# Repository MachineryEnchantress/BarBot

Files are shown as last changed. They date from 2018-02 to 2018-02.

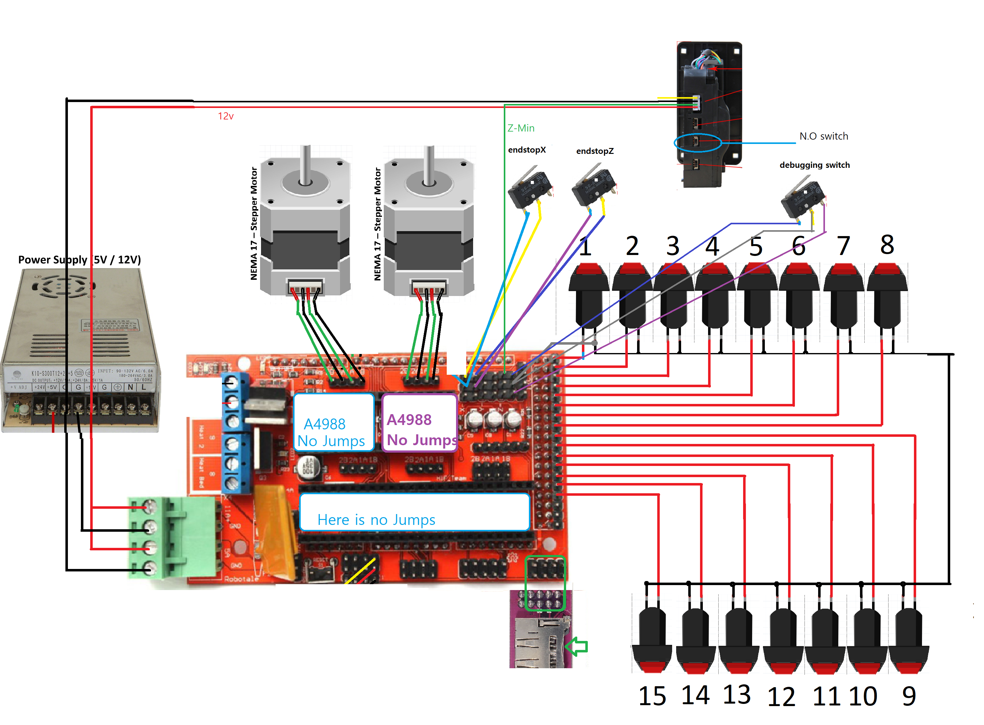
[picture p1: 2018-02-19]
Wiring Diagram.png

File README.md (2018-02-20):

# Naomi Wu's BarBot
An Automated Bartender powered by Arduino  
BarBot

Based on the work of Lukas Šidlauskas:  
https://create.arduino.cc/projecthub/sidlauskas/barbot-cocktail-mixing-robot-0318aa  
https://github.com/sidlauskaslukas/barbot

[BarBot Build Video 1](https://youtu.be/aKa0YGDu1KI)  
BarBot Build Video 1  

[BarBot Build Video 2](https://youtu.be/N1LVktHzpnw)  
BarBot Build Video 2  

[BarBot Build Video 3- Demo](https://youtu.be/aPoAVoNNvHs)  
BarBot Build Video 3

## About

For my BarBot I wanted to make sure it was rock-solid reliable in a crowded bar environment so eliminated the touchscreen menus and wireless connectivity present in other versions of this project. Nearly any error can be dealt with by simply power cycling the device. Since there is no Raspberry Pi or SBC there is no risk of corruption when this is done. 

16 popular drinks (15 alcoholic and 1 non-alcoholic for non-drinkers and so that children can participate with supervision) are available from 16 arcade style buttons. A printed menu lists what button number corresponds to which drink.

Since the BarBot is designed for a working bar- and yes even in Shenzhen we are subject to surprise health inspections I had to do without pumps or difficult to clean feed lines. All of the components that require nightly cleaning are the same that bar staff are already accustomed to cleaning- spirit measures and bar mats. All drive components and bearings have been moved from under the pour spouts to well above or behind so there is no risk of an accumulation of sugar-rich liquids gumming up hard to clean moving parts of the machine or attracting vermin.

This BarBot is a functional novelty- it's something fun for visitors to play with. Perfect for my home city of Shenzhen where a large number of patrons are tech professionals. It is not secured for true commercial use- and with a bar full of half-drunk hardware engineers it would be pointless to try. In this case, it's better to rely on good faith then pretend you could stop them if challenged. Patrons could still manually press their cups to the spirit measures to manually dispense alcohol if they wanted to- but they could also reach over the bar and steal liquor while the bartender's back was turned. So far none have because why ruin the fun when there's no "hack" in doing so? If you really wanted to, a clear acrylic panel could be added to the front to prevent any manual dispensing, but it's really a lot less fun that way.

Portion control and payment is handled via an inexpensive arcade token acceptor. A customer can pay the bartender for a cup of ice and a token. When the correct token is inserted into the BarBot a contact is momentarily closed. The customer then has 60 seconds to press a drink selection button. That same contact can be closed with the key switch, in which case no tokens are needed for any orders while the switch is in that position.

Barbots of this configuration typically use either a servo or a stepper motor with a lead screw to depress the spirit measure spout depending on the type of dispenser it is. My code changes allow for either as RAMPS boards can control both steppers and a servo.

In the build and demonstration videos, you'll see that the full 25ml "shot" the spirit measure contains is usually only partially dispensed. This is because the actual shot size is defined in the code as a function of how long the spout is depressed. This allows for finer tuning of the drink flavor and portion size which would not be possible if only 25ml increments were used.

This BarBot was designed to be easy to build with off-the-shelf OpenBuilds components, V-Slot aluminum extrusion, and low-cost 3D printer parts. The heart of the BarBot is a standard Arduino Mega, RAMPS 1.4/1.5 and A4988 stepper driver combination as used in many 3D printers.

BarBot<BR>
See [Build Guide](https://github.com/sexycyborg/BarBot/blob/master/BarBotDrwMk01.PDF). 
  *Guide and SolidWorks CAD drawings courtesy of [Vexelius](https://www.thingiverse.com/Vexelius/).*

## BOM
[1x Arduino Mega 2560](http://reprap.org/wiki/Arduino_Mega)  
[1x RAMPS 1.4](http://reprap.org/wiki/RAMPS_1.4)/[1.5](http://reprap.org/wiki/RAMPS_1.5)  
[2x A4988 Stepper Driver](http://reprap.org/wiki/A4988)  
[Available as a kit](https://www.gearbest.com/kits/pp_228312.html?lkid=11066669)

1x [RAMPS 1.4/1.5 SD Card Reader](http://amzn.to/2EYiyeb)

[10x10 Drag Chain](http://amzn.to/2ECHM3W)  
 2 Meters 

[V-Slot® 20x80 Linear Rail](http://openbuildspartstore.com/v-slot-20x80-linear-rail/)  
 3x1200mm (Two vertical risers and one horizontal carriage rail)  
 2x1160mm (Lower brace, shelf for bar mat)

[V-Slot® 20x40 Linear Rail](http://openbuildspartstore.com/v-slot-20x40-linear-rail/)  
1x 1200mm (Horizontal rail for drag chain)  
2x 600mm (Horizontal legs)

1x [V-Slot® NEMA 17 Linear Actuator Bundle](http://openbuildspartstore.com/v-slot-nema-17-linear-actuator-bundle-lead-screw/)  
500mm (400mm is better if you can get it or make it yourself)

1x [V-Slot Gantry Set](http://openbuildspartstore.com/v-slot-gantry-set/)  
20mm - 80mm (Universal)  
Delrin Solid V Wheels

1x [Motor Mount Plate - NEMA 17 Stepper Motor](http://openbuildspartstore.com/motor-mount-plate-nema-17-stepper-motor/)

1x [Idler Pulley Plate](http://openbuildspartstore.com/idler-pulley-plate/)

1x [Smooth Idler Pulley Kit](http://openbuildspartstore.com/smooth-idler-pulley-kit/)  

[GT2-2M Timing Belt](http://openbuildspartstore.com/gt2-2m-timing-belt/)  
3 Meters

1x [GT2-2M Timing Pulley - 20 Tooth](http://openbuildspartstore.com/gt2-2m-timing-pulley-20-tooth/)

2x [NEMA 17 Stepper Motor](http://openbuildspartstore.com/nema-17-stepper-motor/)  

30x [Black Angle Corner Connector](http://openbuildspartstore.com/black-angle-corner-connector/)

[Openbuilds Low Profile Screws](http://openbuildspartstore.com/low-profile-screws-m5/)  
60x M5\*8  
4x M5\*40  
6x M5\*25  
4x M5\*15  

[Aluminum Spacer](http://openbuildspartstore.com/aluminum-spacers/)  
4x 3mm  
4x 6mm 

50x [Tee Nuts](http://openbuildspartstore.com/tee-nuts-25-pack/)

50x [Drop In Tee Nuts](http://openbuildspartstore.com/drop-in-tee-nuts/) 

30x [Nylon Insert Hex Locknut - M5](http://openbuildspartstore.com/nylon-insert-hex-locknut-m5/)  

[Slot Cover™ / Panel Holder](http://openbuildspartstore.com/slot-cover-panel-holder/)  
1250mm

2x [Bar mat](http://amzn.to/2Eo2QvR)

#### Control Box
[V-Slot® 20x20 Linear Rail](http://openbuildspartstore.com/v-slot-20x20-linear-rail/)  
530mm x 4  
165mm x 5  
130mm x 4  
(All with 5mm threaded ends)

8x [Cube Corner Connector](http://openbuildspartstore.com/cube-corner-connector/)  

25x M5*15 [Openbuilds Low Profile Screws](http://openbuildspartstore.com/low-profile-screws-m5/)

1x [Coin Acceptor](https://item.taobao.com/item.htm?id=540305747207)  
(Or similar if you modify the lower lasercut panel to fit)  

16x [27x27 Illuminated Arcade Buttons](https://www.aliexpress.com/store/product/27-27mm-quadrate-LED-Light-Illuminated-Full-Colors-Push-Button-With-Micro-Switch-Master-Arcade-DIY/1960309_32559164401.html)

1x [22mm Emergency Stop Push Button Switch 12V DC LED Illuminated (or similar)](http://amzn.to/2Chvvgb)

1x [22mm Key Selector Switch](http://amzn.to/2ErJs0M)

1x [Power Socket Switch IEC 320 C14](http://amzn.to/2HcuYjs)

1x [12v Power Supply, 150w (Part No. MS-150-12 or similar)](https://www.aliexpress.com/item/MS-150-12-mini-size-12-5a-led-psu-150w-12v-power-supply/32663431069.html)

1x [Ribbon cable to 18 pin connector 40CM long (Optional but helpful)](https://item.taobao.com/item.htm?id=520267411024)

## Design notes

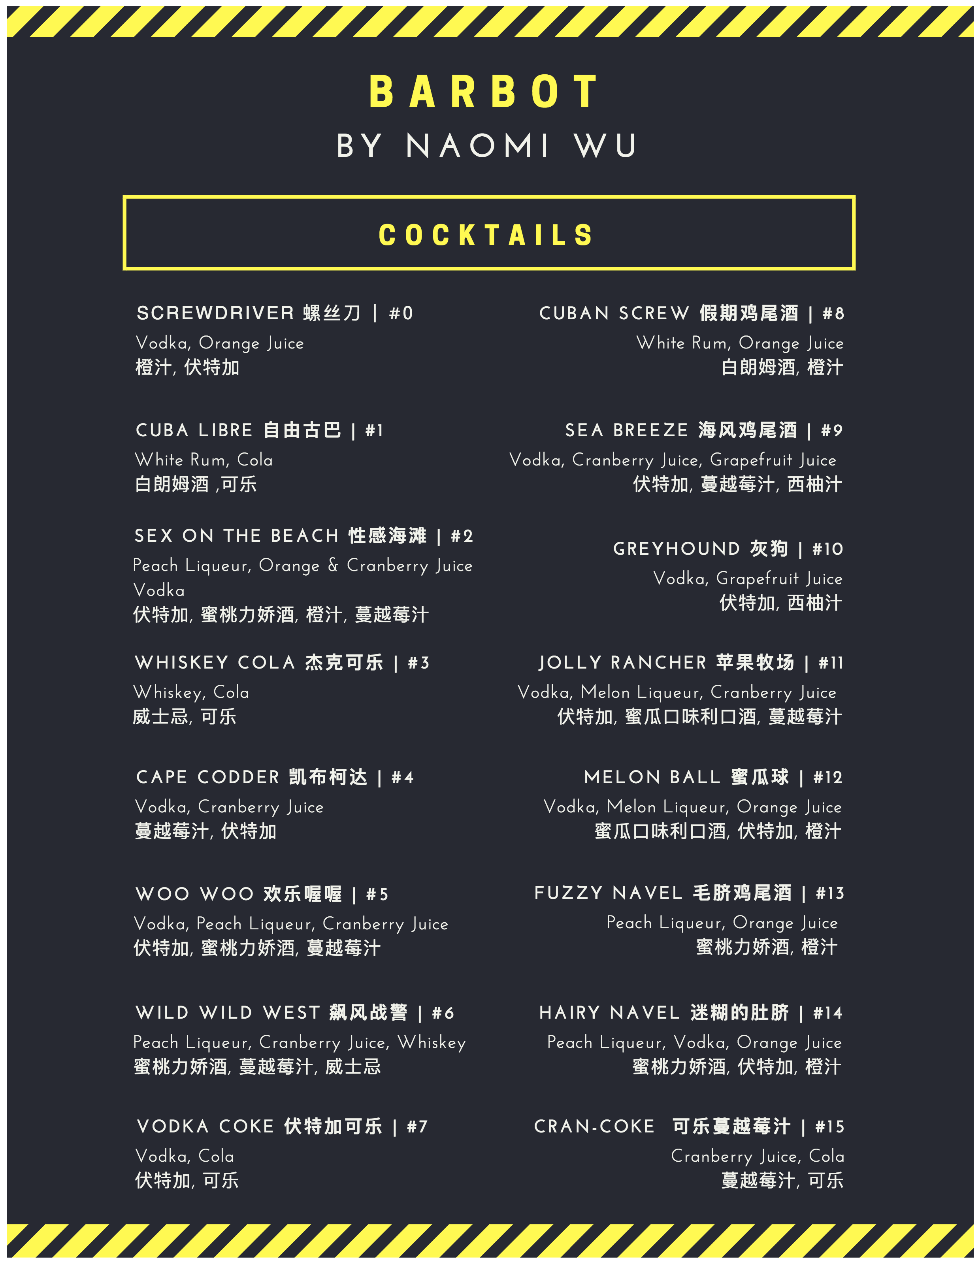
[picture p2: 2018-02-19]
Menu.png

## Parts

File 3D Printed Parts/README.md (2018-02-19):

# Naomi Wu's BarBot
An Automated Bartender powered by Arduino  

All parts can be printed in PLA at 2mm layer height, 30% infill.

## Additional 3D Files Required:

[Quick Release RAMPS Holder for T-Slot Profile](https://www.thingiverse.com/thing:2169986)  

[2020 Cable Zip Tie Mount for M5x10 screws (optional fins)](https://www.thingiverse.com/thing:2486032)

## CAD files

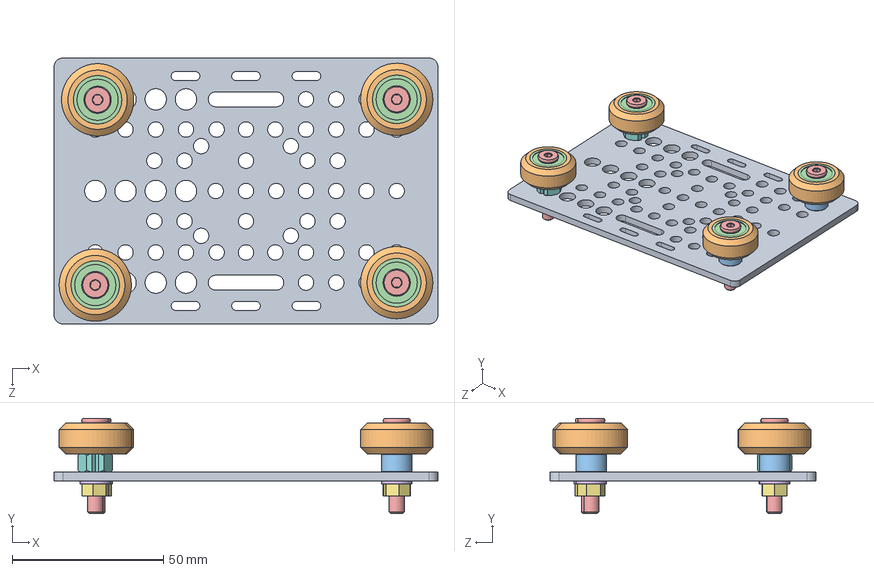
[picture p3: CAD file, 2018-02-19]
SolidWorks/Dispenser Carriage.SLDASM
127.0 x 31.5 x 88.0 mm
V-Slot Gantry Plate 20-80mm
Solid V Wheel x 4
Aluminum Spacer 6mm x 2
Ball Bearing 5 x 16 x 5 x 8
Low Profile Screw M5 x 4
STDWasher x 4
STDNut x 4
Eccentric Spacer 6mm x 2

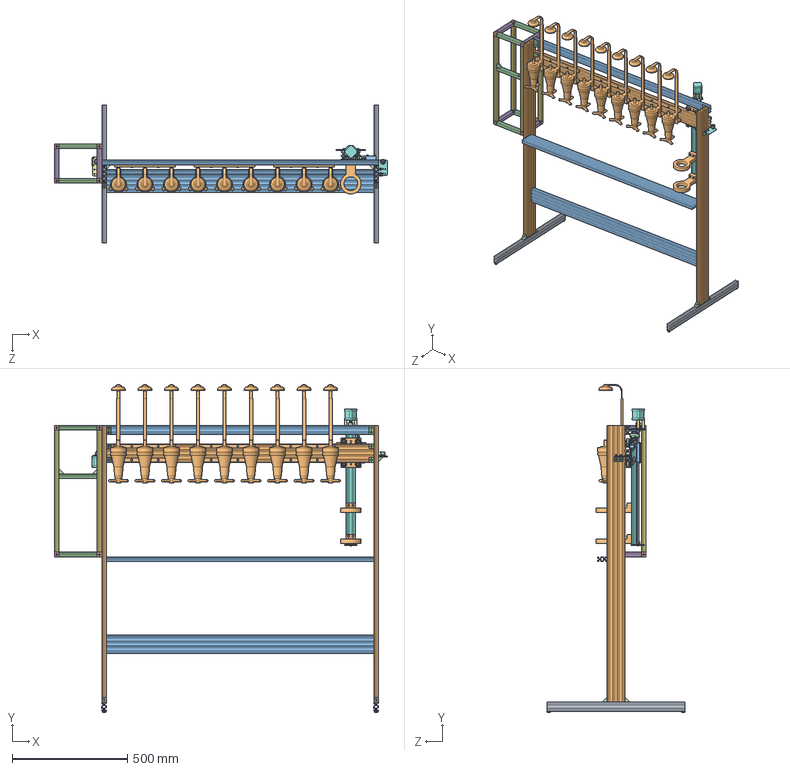
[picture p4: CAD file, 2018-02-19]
SolidWorks/BarBot.SLDASM
1444.5 x 1423.2 x 600.0 mm
V-Slot 20x40x600 x 2
V-Slot 20x80x1200 x 3
V-Slot 20x40x1200
Black Angle Corner Connector x 20
Tee Nut x 12
Low Profile Screw M5 x 42
RubberPad x 4
Idler Pulley Plate
STDNut x 12
STDWasher x 12
Aluminum Spacer 6mm x 7
Smooth Idler Pulley Wheel
Ball Bearing 5 x 16 x 5 x 18
Nylon Spacer 0.125in
Motor Mount Plate Nema 17
Nema 17 Stepper Motor x 2
GT2 Timing Pulley 20 Tooth
Bar Butler x 3
V-Slot 20x80x1160 x 2
V-Slot 20x20x165 x 5
Cube Corner Connector x 8
V-Slot 20x20x130 x 4
V-Slot 20x20x530 x 4
Self Tapping Screw x 4
Socket Head Cap Screw M3 x 3
Nylon Insert Lock Nut M5 x 6
Threaded Rod Plate Nema 17 x 2
Ball Bearing 8 x 16 x 5 x 2
Shim Washer 8mm x 2
Lock Collar 8mm x 2
Aluminum Spacer 1.5in x 3
Flexible Coupling 5mm x 8mm
8mm leadscrew 520mm
V-Slot Gantry Plate 20-80mm x 2
Spacer Block x 2
Solid V Wheel x 8
Precision Shim 10 x 5 x 1 x 8
8mm Acme Nut Block
Eccentric Spacer 6mm x 2
V-Slot 20x40x500 Linear Rail
Aluminum Spacer 3mm x 8
CupRing x 2
XAxis Endstop Holder
RAMPSEndStop x 2
Button Head Socket Cap Screw M3 x 4
ZAxis Endstop Holder

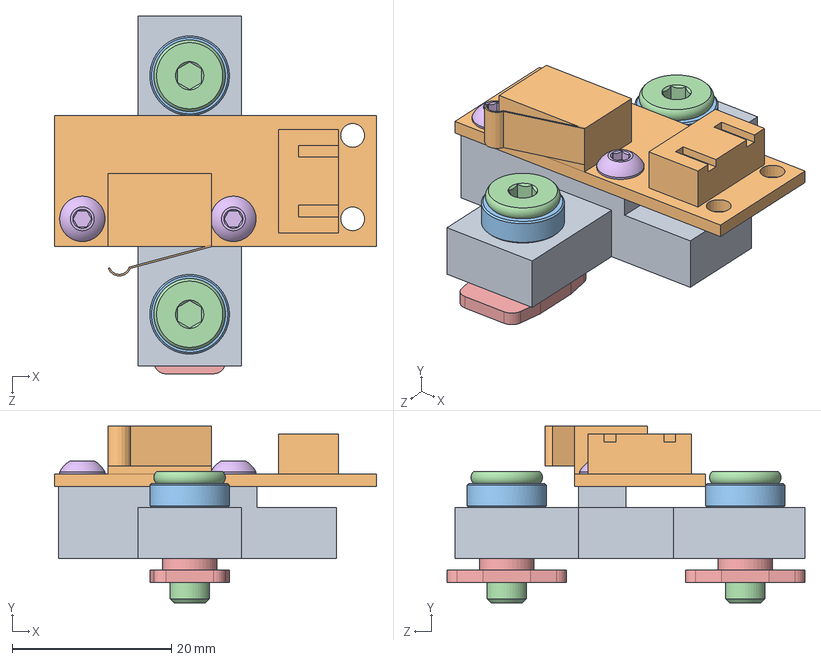
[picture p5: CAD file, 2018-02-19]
SolidWorks/Z-Axis Endstop.SLDASM
40.5 x 22.2 x 45.0 mm
ZAxis Endstop Holder
RAMPSEndStop
Aluminum Spacer 3mm x 2
Low Profile Screw M5 x 2
Tee Nut x 2
Button Head Socket Cap Screw M3 x 2

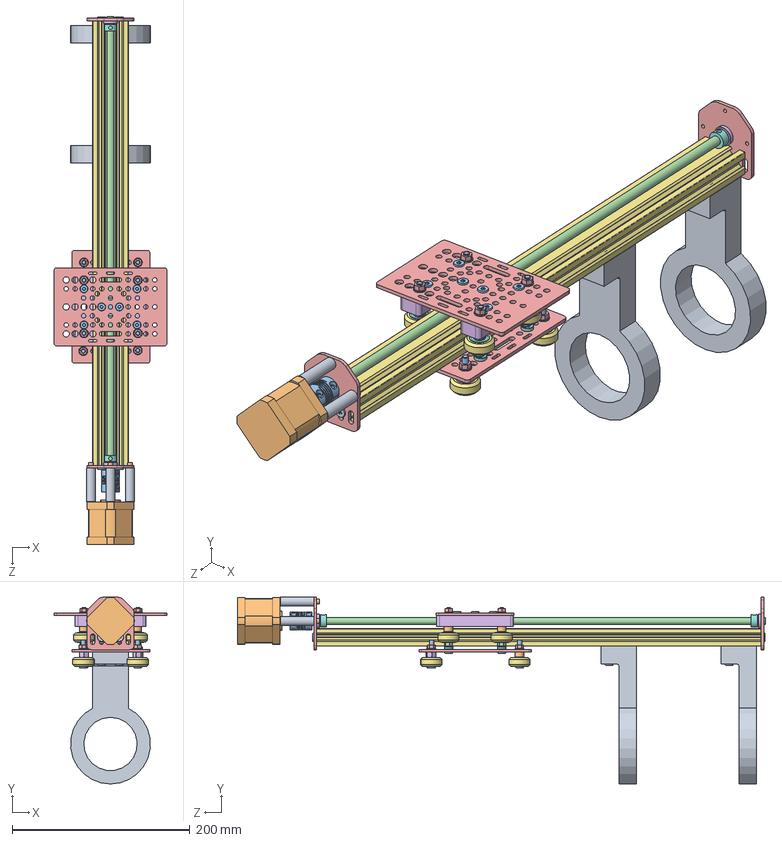
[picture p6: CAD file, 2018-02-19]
SolidWorks/Dispenser Actuator.SLDASM
127.0 x 210.3 x 594.1 mm
Self Tapping Screw x 4
Socket Head Cap Screw M3 x 3
Low Profile Screw M5 x 18
Nylon Insert Lock Nut M5 x 6
Threaded Rod Plate Nema 17 x 2
Ball Bearing 8 x 16 x 5 x 2
Shim Washer 8mm x 2
Lock Collar 8mm x 2
Aluminum Spacer 1.5in x 3
Nema 17 Stepper Motor
Flexible Coupling 5mm x 8mm
8mm leadscrew 520mm
V-Slot Gantry Plate 20-80mm x 2
Spacer Block x 2
Solid V Wheel x 8
Ball Bearing 5 x 16 x 5 x 16
Precision Shim 10 x 5 x 1 x 8
Aluminum Spacer 6mm x 6
8mm Acme Nut Block
STDWasher x 8
STDNut x 8
Eccentric Spacer 6mm x 2
V-Slot 20x40x500 Linear Rail
Aluminum Spacer 3mm x 4
CupRing x 2
Tee Nut x 4

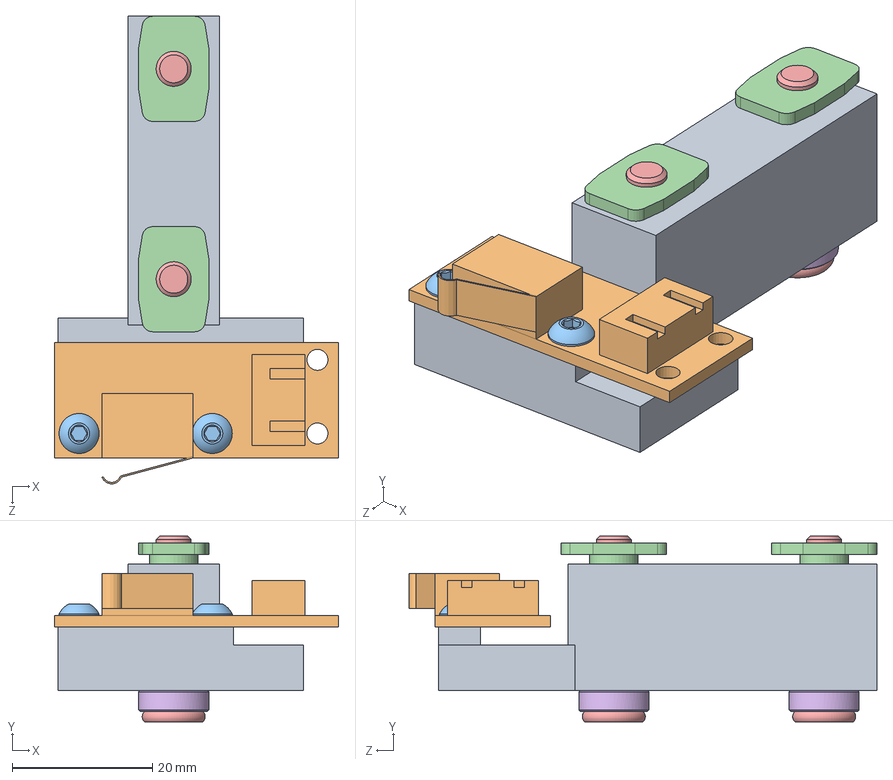
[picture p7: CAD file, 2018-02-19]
SolidWorks/X-Axis Endstop.SLDASM
40.5 x 26.5 x 66.7 mm
XAxis Endstop Holder
RAMPSEndStop
Button Head Socket Cap Screw M3 x 2
Tee Nut x 2
Low Profile Screw M5 x 2
Aluminum Spacer 3mm x 2

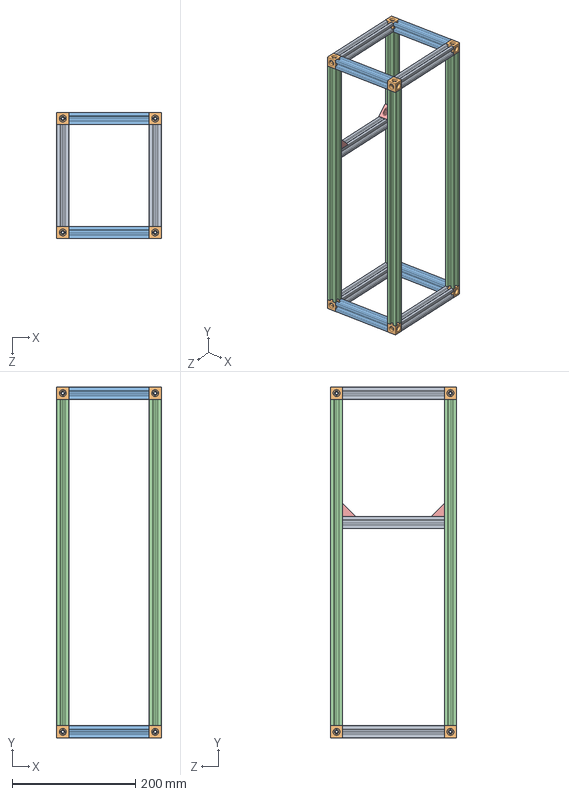
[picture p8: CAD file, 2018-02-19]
SolidWorks/Control Box.SLDASM
170.0 x 570.0 x 205.0 mm
V-Slot 20x20x165 x 5
Cube Corner Connector x 8
V-Slot 20x20x130 x 4
V-Slot 20x20x530 x 4
Black Angle Corner Connector x 2

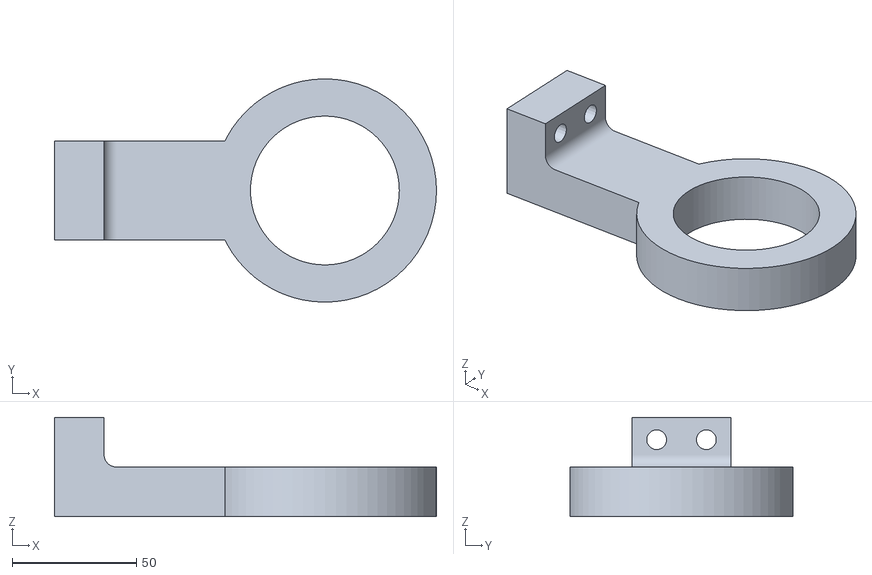
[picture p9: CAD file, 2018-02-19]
3D Printed Parts/Cup Ring.stl
154.0 x 90.0 x 40.0

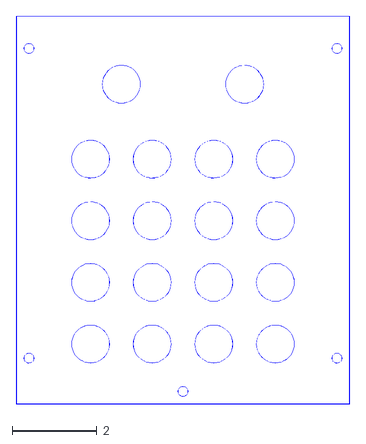
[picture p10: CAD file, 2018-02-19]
Laser Cut Panels/233mm x 200mm- Upper Front v1.dxf
7.88 x 9.17

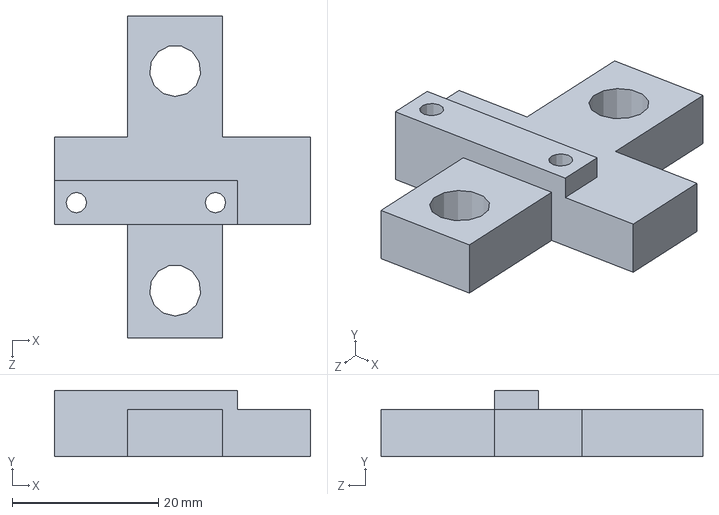
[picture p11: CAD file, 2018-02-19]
SolidWorks/ZAxis Endstop Holder.SLDPRT
35.0 x 9.05 x 44.0 mm

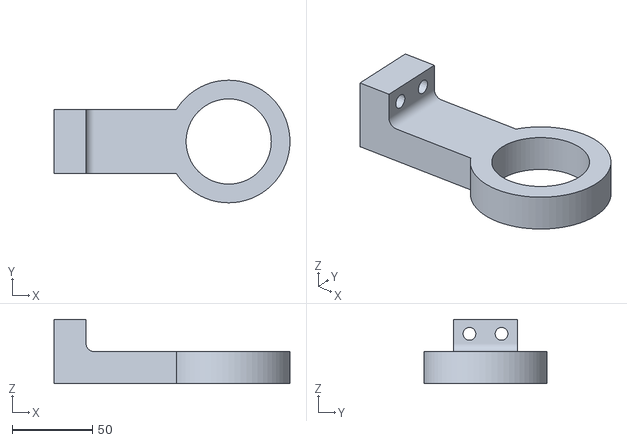
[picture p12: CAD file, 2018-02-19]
3D Printed Parts/Spirit Measure Ring.stl
147.2 x 76.5 x 40.0

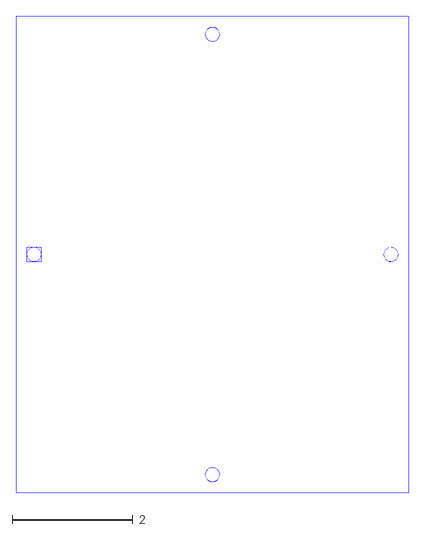
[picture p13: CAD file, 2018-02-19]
Laser Cut Panels/200mm x 165mm- Top v1.dxf
6.50 x 7.88

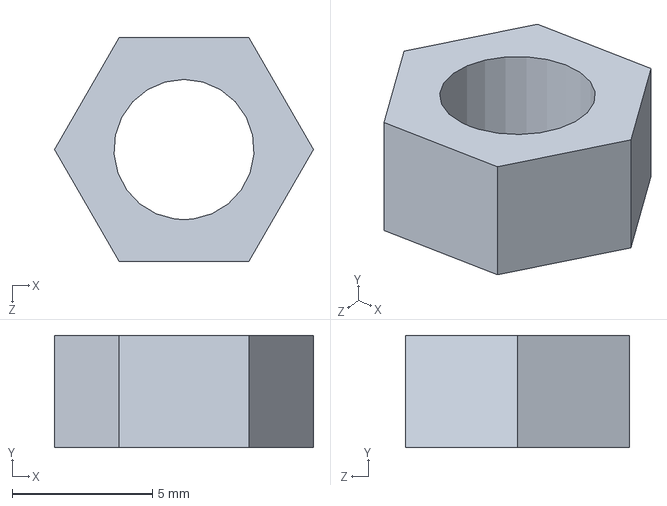
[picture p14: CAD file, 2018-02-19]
SolidWorks/STDNut.SLDPRT
9.24 x 4.00 x 8.00 mm

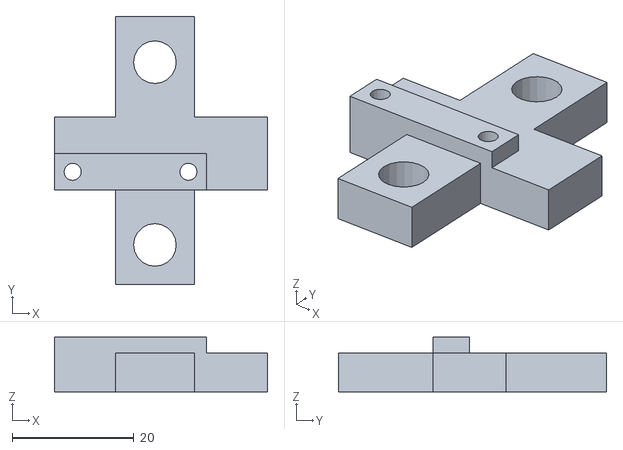
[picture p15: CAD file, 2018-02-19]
3D Printed Parts/Z-Axis End-Stop Switch Holder.stl
35.0 x 44.0 x 9.00

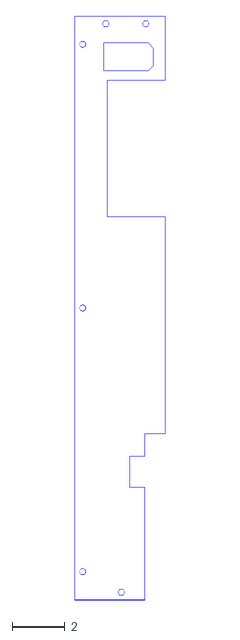
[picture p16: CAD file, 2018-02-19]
Laser Cut Panels/565mm x 87.5mm Rear Side v2.dxf
3.45 x 22.2

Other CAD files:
SolidWorks/XAxis Endstop Holder.SLDPRT
3D Printed Parts/Z-Axis Motor Drag Chain Attachment.stl
Laser Cut Panels/332mm x 200mm- Front Lower v1.dxf
3D Printed Parts/X-Axis End-Stop Switch Holder.stl
Laser Cut Panels/565mm x 165mm- Side v1.dxf
Laser Cut Panels/565mm x 200mm- Back v1.dxf
SolidWorks/BarBot.SLDPRT
SolidWorks/CupRing.SLDPRT
SolidWorks/RAMPSEndStop.SLDPRT
SolidWorks/RubberPad.SLDPRT
SolidWorks/STDWasher.SLDPRT
SolidWorks/V-Slot 20x20x130.SLDPRT
SolidWorks/V-Slot 20x20x165.SLDPRT
SolidWorks/V-Slot 20x20x530.SLDPRT
SolidWorks/V-Slot 20x40x1200.SLDPRT
SolidWorks/V-Slot 20x40x600.SLDPRT
SolidWorks/V-Slot 20x80x1160.SLDPRT
SolidWorks/V-Slot 20x80x1200.SLDPRT

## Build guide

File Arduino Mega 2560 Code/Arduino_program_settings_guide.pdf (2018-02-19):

BARBOT Arduino setting Guide.

1. Install the Arduino IDE.
2. Install necessary libraries to the Arduino IDE

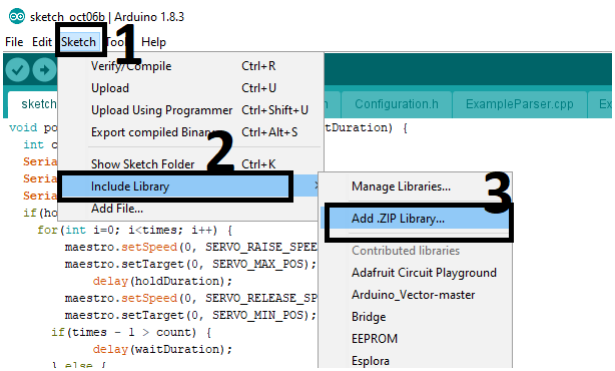
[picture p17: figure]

- Add “Arduino_Vector-master.zip”
- Add “Json_Streaming_Parser-1.0.5.zip”

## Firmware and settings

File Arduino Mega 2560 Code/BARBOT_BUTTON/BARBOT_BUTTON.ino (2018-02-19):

#include "JsonInit_.h"

#include "AccelStepper.h"
#include "Configuration.h"
#include <Vector.h>
#include <Servo.h>

/*-------------------coin accepter time-------------*/
unsigned long coin_accepted_time_old = 0;
int coin_accepted = 0;



const int chipSelect = 53;

JsonInit_ mJson(chipSelect);

Vector<INGREDIENTS> v_i;
Vector<RECIPES> v_re;

AccelStepper stepper(X_INTERFACE_TYPE, X_STEP_PIN, X_DIR_PIN); // Define a stepper and the pins it will use
AccelStepper stepperZ(Z_INTERFACE_TYPE, Z_STEP_PIN, Z_DIR_PIN); // Define a stepper and the pins it will use



void serial_init(){
  Serial.begin(9600);
  while (!Serial) {
    ; // wait for serial port to connect. Needed for native USB port only
  }
  Serial.println("serial port inited");
}


void homeXAxis() {
    
  int endStopState = digitalRead(X_ENDSTOP_PIN); 
   while (endStopState == HIGH) {
    stepper.moveTo(100);
    stepper.setSpeed(X_HOME_SPEED);
    stepper.runSpeed();
   endStopState = digitalRead(X_ENDSTOP_PIN);  
  }  

  stepper.moveTo(stepper.currentPosition() - 50);
   while (stepper.distanceToGo() != 0) {
    stepper.setSpeed(X_PARK_SPEED * -1);
    stepper.runSpeed();      
  }
  
  endStopState = digitalRead(X_ENDSTOP_PIN);  
  while (endStopState == HIGH) {
     stepper.moveTo(100);
    stepper.setSpeed(X_PARK_SPEED);
    stepper.runSpeed();   
    endStopState = digitalRead(X_ENDSTOP_PIN);
  }

  stepper.setCurrentPosition(0); 
}


void moveXTo(int pos) {  
  
  Serial.print("X goes to: ");
  Serial.println(pos);
  
  if(pos <= 0 && pos >= X_MAX_POS) {
    stepper.setAcceleration(X_ACCELERATION);
    stepper.moveTo(pos);
      if(pos < stepper.currentPosition()) {
      
        stepper.setSpeed(-100);
      } else {
       
        stepper.setSpeed(100);
      }
    while(stepper.distanceToGo() != 0) {
      stepper.run(); 
    }
  } else {
    Serial.println("Position should be between -4995 and 0");
  }
}


void button_init(){    
  pinMode(16, INPUT_PULLUP); 
  pinMode(17, INPUT_PULLUP); 
  pinMode(23, INPUT_PULLUP); 
  pinMode(25, INPUT_PULLUP); 

  pinMode(27, INPUT_PULLUP); 
  pinMode(29, INPUT_PULLUP); 
  pinMode(31, INPUT_PULLUP); 
  pinMode(33, INPUT_PULLUP); 

  pinMode(35, INPUT_PULLUP); 
  pinMode(37, INPUT_PULLUP); 
  pinMode(39, INPUT_PULLUP); 
  pinMode(41, INPUT_PULLUP); 

  pinMode(43, INPUT_PULLUP); 
  pinMode(45, INPUT_PULLUP); 
  pinMode(47, INPUT_PULLUP);  
  pinMode(32, INPUT_PULLUP);  
  
  pinMode(18, INPUT_PULLUP); // Coin Accepter signal input
  pinMode(19, INPUT_PULLUP); // Debugging button
  
}
  
void setup() {
  
  // Open serial communications and wait for port to open:
  pinMode(24, OUTPUT);   // enable A4988
  digitalWrite(24, LOW); // enable A4988

  pinMode(30, OUTPUT);   // enable A4988
  digitalWrite(30, LOW); // enable A4988

  
  serial_init();
  button_init();
  
  
  mJson.Init_("INGRED~1.JSO","RECIPE~1.JSO");
  Serial.println("Json Testing-----------------------");

      
  v_re = mJson.listener_RECIPE.vi_recipe_item;
  v_i  = mJson.listener_INGRED.vi;

  Serial.println(v_re.size());
//  mJson.Init_("ingredients.json","recipes.json");
  stepper.setMaxSpeed(X_MAX_SPEED); // Sets the maximum speed the X axis accelerate up to
  stepperZ.setMaxSpeed(Z_MAX_SPEED); // Sets the maximum speed the Z axis accelerate up to
  pinMode(Z_ENDSTOP_PIN, INPUT_PULLUP); // Initialize Z- endstop pin with the internal pull-up resistor enabled 
  pinMode(X_ENDSTOP_PIN, INPUT_PULLUP); // Initialize X- endstop pin with the internal pull-up resistor enabled
  pinMode(14, INPUT_PULLUP);// for Stop Interrupt
  pinMode(15, INPUT_PULLUP);// for Home z, x 
  homeZAxis(); // Return the Z axis to it's home position at the startup
  homeXAxis(); // Return the X axis to it's home position at the startup


  coin_accepted = 0;
}
void coin_acceptor_handler(){
  if (digitalRead(18) == 0){ // coin accepted 
    delay(100); // --------------------------------------- coin accepting delay time
    coin_accepted = 1;
    coin_accepted_time_old = millis();
  }
}
void loop() {
 
  unsigned long current_time = 0;  
  coin_acceptor_handler();  
  button_scheduler();
  current_time = millis();
  if ((current_time - coin_accepted_time_old) > 60000) // no reponse for 60s
  {
    coin_accepted_time_old = current_time;
    coin_accepted = 0;
  }
  delay(5);
}


int get_button_state(){      
  if (!digitalRead(16)) return 0;
  if (!digitalRead(17)) return 1;
  if (!digitalRead(23)) return 2;
  if (!digitalRead(25)) return 3;
  
  if (!digitalRead(27)) return 4;
  if (!digitalRead(29)) return 5;
  if (!digitalRead(31)) return 6;
  if (!digitalRead(33)) return 7;
  
  if (!digitalRead(35)) return 8;
  if (!digitalRead(37)) return 9;
  if (!digitalRead(39)) return 10;
  if (!digitalRead(41)) return 11;  

  if (!digitalRead(43)) return 12;  
  if (!digitalRead(45)) return 13;  
  if (!digitalRead(47)) return 14;    
  if (!digitalRead(32)) return 15;    
  
  return 100;
}

void get_RecipeData(int butState){
  int bufIndex = butState;
  for (int i = 0; i < v_re.size(); i++){
    if(v_re[i].id == 0 && v_re[i].amount == 0) {bufIndex--; continue;}
    if (bufIndex < 0) return;
    if (bufIndex == 0){
      moveXTo(v_i[v_re[i].id - 1].coordinate);  
      pourZ(v_re[i].amount/ 20,v_i[v_re[i].id - 1].hold, v_i[v_re[i].id - 1].wait);      
    }
  }
}

void button_scheduler(){   
 if (digitalRead(19) &&!coin_accepted) return;  
 int butState = get_button_state();
 if (butState == 100) return; 
 coin_accepted = 0; 
 get_RecipeData(butState); 
 moveZTo(0); // Return the Z axis to it's home position at the startup
 Serial.println("return to x home");
 moveXTo(0); // Return the X axis to it's home position at the startup

}

void homeZAxis() {          
  
        int endStopState = digitalRead(Z_ENDSTOP_PIN);         
        while (endStopState == HIGH) {
        
          stepperZ.moveTo(50);
          stepperZ.setSpeed(Z_HOME_SPEED);
          stepperZ.runSpeed();
          endStopState = digitalRead(Z_ENDSTOP_PIN);  
        }  
        
        stepperZ.moveTo(stepperZ.currentPosition() - 25);
        
        while (stepperZ.distanceToGo() != 0) {        
          stepperZ.setSpeed(Z_PARK_SPEED * -1);
          stepperZ.runSpeed();            
        }
        endStopState = digitalRead(Z_ENDSTOP_PIN);

      
        while (endStopState == HIGH) {
          stepperZ.moveTo(50);        
          stepperZ.setSpeed(Z_PARK_SPEED);
          stepperZ.runSpeed();   
          endStopState = digitalRead(Z_ENDSTOP_PIN);
        }  
       
        stepperZ.setCurrentPosition(0); 
      }
      
void moveZTo(int pos) {    
            
      Serial.print("Z goes to: ");
      Serial.println(pos);    
      
      stepperZ.setAcceleration(Z_ACCELERATION);
      stepperZ.moveTo(pos);
      
      if(pos < stepperZ.currentPosition()) {
            stepperZ.setSpeed(-100);
          } else {
            stepperZ.setSpeed(100);
          }
        while(stepperZ.distanceToGo() != 0) {
          stepperZ.run(); 
        }      
    }
 
void pourZ(int times, int holdDuration,int waitDuration) {
        int count = 0; // Pour counter 
        if(holdDuration > 0 && waitDuration > 0) {
          for(int i=0; i<times; i++) {            
              moveZTo(Z_MAX_POS);
              delay(holdDuration - HOLD_DELAY_IN_Z_MAX);              
              moveZTo(0); // Return the Z axis to it's home position at the startup
             if(times - 1 > count) {
                      delay(waitDuration);
                } else {
                      delay(DELAY_BETWEEN_INGREDIENTS);
                }
              count++;
            }
        } else {
          Serial.println("Hold and wait duration parameters cannot be lower than or equal to 0");
        }
}

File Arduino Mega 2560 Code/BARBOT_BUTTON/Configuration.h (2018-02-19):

#ifndef CONFIGURATION_H
#define CONFIGURATION_H

#define maestroSerial SERIAL_PORT_HARDWARE_OPEN

// Stepper driver
#define X_INTERFACE_TYPE 1 // Stepper motor interface type
#define X_STEP_PIN 26 // Stepper driver step pin
#define X_DIR_PIN 28 // Stepper driver dir pin

// Stepper motor
#define X_PARK_SPEED 150 // Parking speed
#define X_HOME_SPEED 700 // Homing speed
#define X_MAX_SPEED 1000 // The maximum speed in steps per second the X axis accelerate up to
#define X_ACCELERATION 3000 // Acceleration/deceleration rate in steps per second per second
#define X_MAX_POS -4995 // The maximum position for the X axis

// Stepper driver
#define Z_INTERFACE_TYPE 1 // Stepper motor interface type
#define Z_STEP_PIN 36 // Stepper driver step pin
#define Z_DIR_PIN 34 // Stepper driver dir pin

// Stepper motor
#define Z_PARK_SPEED 150 // Parking speed
#define Z_HOME_SPEED 700 // Homing speed
#define Z_MAX_SPEED 1000 // The maximum speed in steps per second the Z axis accelerate up to
#define Z_ACCELERATION 3000 // Acceleration/deceleration rate in steps per second per second
#define Z_MAX_POS -3000 // The maximum position for the Z axis

/*
  Hold delay time in Z max  = 2250 -  HOLD_DELAY_IN_Z_MAX  

  EX: looking 1 second delay:
   1000 = 2250 - 1250 <<<<=== hold delay in z max should be setted as 1250   
*/
#define HOLD_DELAY_IN_Z_MAX 2250 // max value is 2250



// Servo motor
#define SERVO_MAX_POS 0 // Servo hold position
#define SERVO_MIN_POS 90 // Servo normal position
#define SERVO_RAISE_SPEED 30 // The speed of the servo when travelling from the normal to the hold position
#define SERVO_RELEASE_SPEED 0 // The speed of the servo when travelling from the hold to the normal position

// Endstop
#define X_ENDSTOP_PIN 3 // Endstop pin
#define Z_ENDSTOP_PIN 2 // Endstop pin


// Other
#define TOTAL_ACTIONS 30 // Total number of actions
#define DELAY_BETWEEN_INGREDIENTS 600 // Time duration to wait before travelling to the next ingredient

#endif
